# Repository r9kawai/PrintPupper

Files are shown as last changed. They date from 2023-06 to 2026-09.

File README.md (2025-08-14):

# PrintPupper  
## Release v0.2 2025 Aug 14
PrintPupper is an open-source quadruped robot that anyone can build. It is based on Pupper, developed by Stanford University, and has been redesigned to be cheaper and easier to build. With just a 3D printer and inexpensive parts, you can build a full-fledged quadruped robot with 12 joints.  
PrintPupper は誰でも作れるオープンソースの四足歩行ロボットです。スタンフォード大学の開発したPupperを元に、より安価に簡単に作れるよう再設計しました。3Dプリンタと安価な部品だけで12自由度の本格四足ロボを作れます。
  
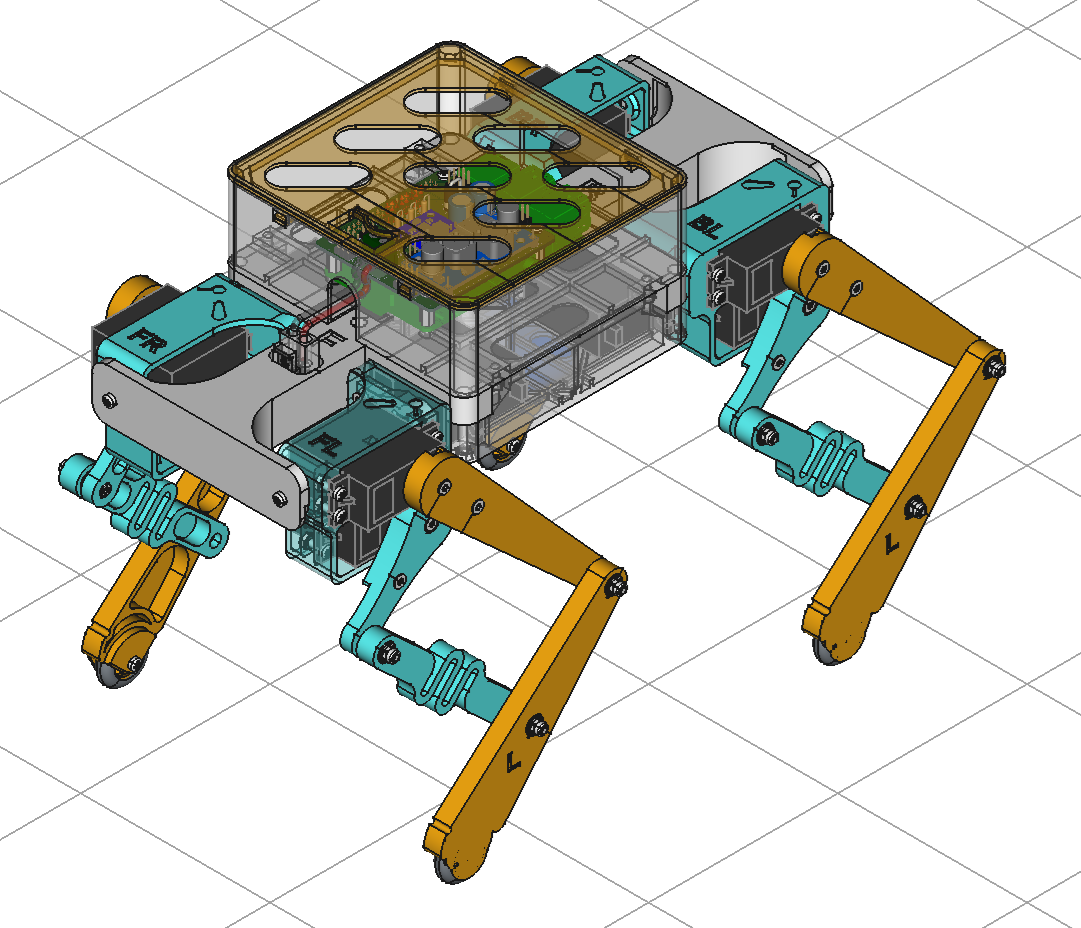
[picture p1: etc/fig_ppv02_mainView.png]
  
  
## printpupper.com  
[https://www.printpupper.com/](https://www.printpupper.com/)  
This portal site explains the assembly procedure with detailed figs.
このポータルサイトでは組立手順を詳細な図で説明しています。
  
・3DプリンターとAmazonで容易に入手できる安価な部品だけで作れる。  
・組立手順をWebで詳細に説明。  
・FreeCAD設計データ、KiCAD基板設計データなど全てGitHubで公開。  
・オリジナル設計よりも頑丈で壊れにくい。  
・USBジョイパッド対応。  
・キャリブレーション作業がジョイパッドだけで可能。  
・RC用大容量バッテリー搭載可能で40分の連続歩行。  
・拡張性あり、改造が容易、IMU搭載が可能。  
・Raspberry Pi 3以降または、Raspberry Pi Zero 2 W での作成が可能。  
  
・Can be built using only a 3D printer and inexpensive parts readily available on Amazon.  
・Assembly instructions are explained in detail on the Web.  
・FreeCAD design data, KiCAD board design data, etc. are all available on GitHub.  
・Sturdier and less likely to break than the original design.  
・Compatible with USB joypad.  
・Calibration can be done using only the joypad.  
・Can be equipped with a large-capacity RC battery for 40 minutes of continuous walking.  
・Expandable, easy to modify, and can be equipped with an IMU.  
・Can be built with a Raspberry Pi 3 or later, or a Raspberry Pi Zero 2 W.

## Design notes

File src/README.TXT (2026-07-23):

# If you choose 270deg servo, please "touch _servo_type_270deg"

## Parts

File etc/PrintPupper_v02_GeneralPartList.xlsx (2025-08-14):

PrintPupper_v02_GeneralPartList | 一般部品リスト
Class 分類 | Name | 名称 | Qua / 数量 | in 4leg | in torso | in stand
Servo motor サーボモーター | DS3235 180deg 35kg core less servo | DS3235 180度35KGコアレスサーボ | 12
 | ※ needs the attached metal horn in servo | ※ 付属の金属ホーンが必要
Metal parts 金属部品 | M3 Hex nut | M3 六角ナット | 64 | 48 | 14 | 2
 | M3 Nylon hex nut | M3 ナイロン六角ナット | 12 | 12
 | M3 10mm countersunk hex cap screw | M3 10mm 六角穴皿ボルト | 24 | 24
 | M3 10mm truss-head screw | M3 10mm トラス頭ネジ | 50 | 40 | 8 | 2
 | M3 20mm hex cap screw | M3 20mm 六角穴ボルト | 18 | 12 | 6
 | 693ZZ Ball bearing 3x8x4mm | 693ZZ ボールベアリング | 28 | 28
 | M2.5 8mm screw | M2.5 8mm ねじ | 8 |  | 8
 | M2.5 12mm hex spacer | M2.5 12mm 六角スペーサー | 4 |  | 4
※ in use RaspiZero | M2.5 Hex nut | M2.5 六角ナット | 2 |  | 2
 | Servo horn (Attached in servo) | サーボホーン (サーボ付属品) | 12 | 12
 | M2 8mm hex cap screw (Attached in servo) | M2 8mm 六角穴ボルト (サーボ付属品) | 24 | 24
Rubber parts ゴム部品 | Rubber in Dia 16mm Out 25mm | ゴムグロメット内径16mm外径25mm相当品 | 4
 | equivalent item
PCB parts プリント基板部品 | Main PCB | メイン基板 | 1
 | XL6009 boost back DC-DC converter | XL6009昇降圧DCDCコンバータ | 1
 | Resistor 1k ohm 0.25W | 抵抗 1kオーム 0.25W | 3
 | Electrolytic condenser 2200uF 16V | 電解コンデンサ 2200uF 16V | 2
 | Schottky Barrier Diode 1N5820 | ショットキーバリアダイオード 1N5820 | 1
 | LED red | LED 赤 | 1
 | LED green | LED 緑 | 1
 | LED blue | LED 青 | 1
 | Terminal block 2contact 5.08mm pitch | ターミナルブロック 2端子 5.08mmピッチ | 1
 | Pin header 2.54mm pitch 40pin 1 row | ピンヘッダ 2.54mmピッチ 40ピン 1列 | 2
 | 40(2x20)pin header socket | 40(2x20)ピンヘッダソケット | 1
 | Tamiya bat connecter harness male | タミヤバッテリコネクタハーネス(オス) | 1
CPU board CPUボード | Raspberry Pi "3" or "4" or "Zero 2 W" | ラズベリーパイ 3または4またはZero 2 W | 1
 | ※ Zero W is NG
Battery バッテリー | 2S 7.4v LiPo battery (Tamiya) | 2S 7.4v リポバッテリー タミヤコネクタ | 1
 | 7.2v NiCd Battery Pack Tamiya compatible | 7.4v タミヤニッカドバッテリー互換品
 | 製品例 Choice cases | GOLDBAT 4000mAh 2S 7.4V Lipo TAMIYA Plug
※ Option オプション | MPU6050 accelerometer gyro sensor | MPU6050加速度センサー | 1
Controller コントローラ | エレコム ゲームパッド JC-U3912TBK |  | 1
 | PS4 Controller (DUAL SHOCK4) | PS4 コントローラ (DUAL SHOCK4)
 | ※ Worked with compatible products. | ※ 互換品でも動作しました。
 |  | Total | 282

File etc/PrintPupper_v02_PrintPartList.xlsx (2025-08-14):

PrintPupper_v02_PrintPartList | 印刷部品リスト
File name | Name | 名称 | Qua / 数量
01_print_knee_horn_4pcs.step | Knee horn | 膝ホーン | 4
02_print_upper_leg_4pcs.step | Upper leg | 上脚 | 4
03_print_knee_linkage_4pcs.step | Knee linkage | 膝リンク | 4
04_print_lower_leg_L_2pcs.step | Lower leg L | 下脚R | 2
05_print_lower_leg_R_2pcs.step | Lower leg R | 下脚L | 2
06_print_lower_leg_cap_4pcs.step | Lower leg cap | 下脚キャップ | 4
07_print_coxa_FL_1pcs.step | Coxa FL1 | 股関節FL | 1
08_print_coxa_FR_1pcs.step | Coxa FR1 | 股関節FR | 1
09_print_coxa_BL_1pcs.step | Coxa BL1 | 股関節BL | 1
10_print_coxa_BR_1pcs.step | Coxa BR1 | 股関節BR | 1
11_print_center_torso_1pcs.step | Center torso | 中央胴体 | 1
12_print_front_torso_1pcs.step | Front torso | 前胴体 | 1
13_print_back_torso_1pcs.step | Back torso | 後胴体 | 1
14_print_battery_holder_2pcs.step | Battery holder | バッテリホルダ | 2
15_print_pcb_box_1pcs.step | PCB box | PCB箱 | 1
16_print_pcb_box_lid_1pcs.step | PCB box lid | PCB箱蓋 | 1
17_print_stand_upper_1pcs.step | Stand upper | スタンド上 | 1
18_print_stand_lower_1pcs.step | Stand lower | スタンド下 | 1
19_print_calibration_plate_1pcs.step | Calibration plate | キャリブプレート | 1
 |  | Total | 34

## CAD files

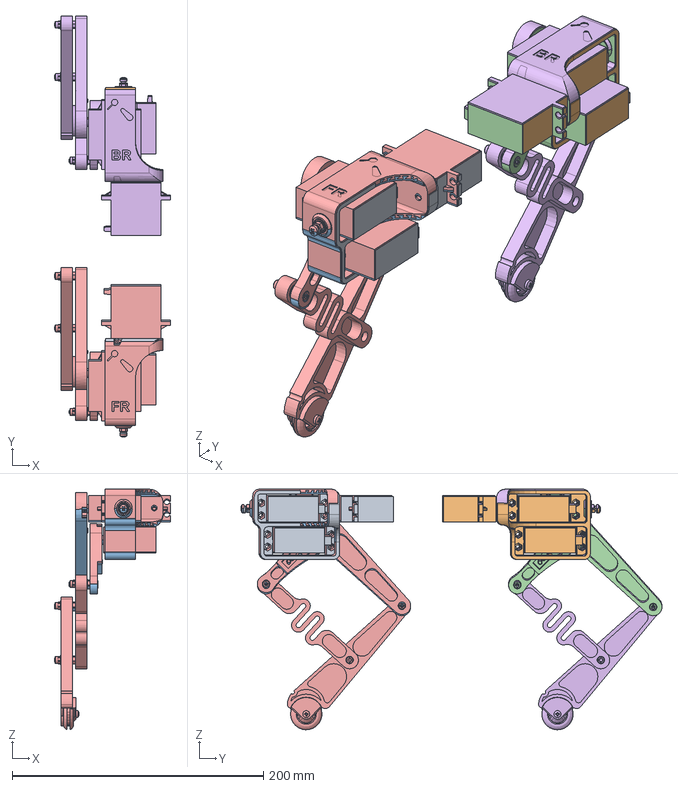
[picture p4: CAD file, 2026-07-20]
freecad/PrintPupper_v02_0_StdAssembly.FCStd
92.6 x 335.1 x 191.6 mm
GeoCheckFR_0
GeoCheckBR_0
GeoCheckFR_1
GeoCheckBR_1
GeoCheckFR_2
GeoCheckBR_2

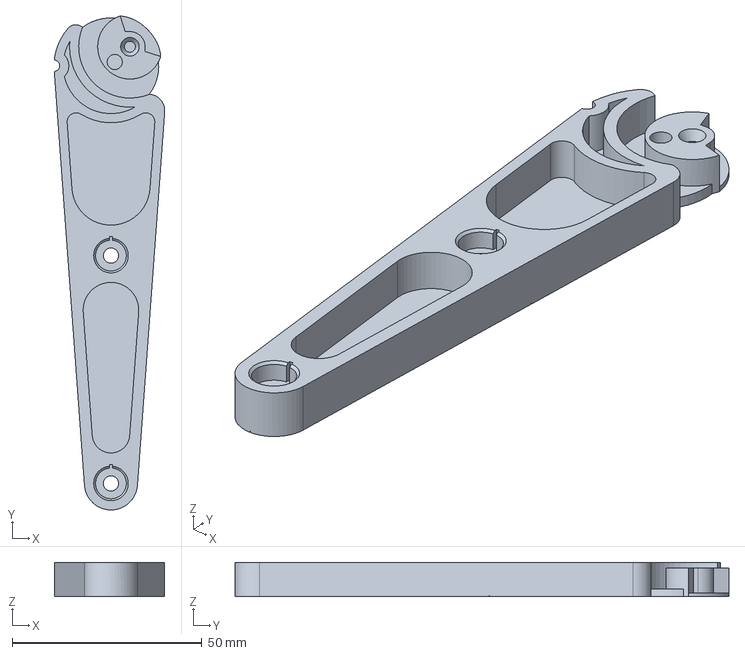
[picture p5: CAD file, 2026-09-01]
freecad/exportSTEP/04_new_print_lower_leg_L_2pcs.step
29.1 x 130.1 x 9.00 mm

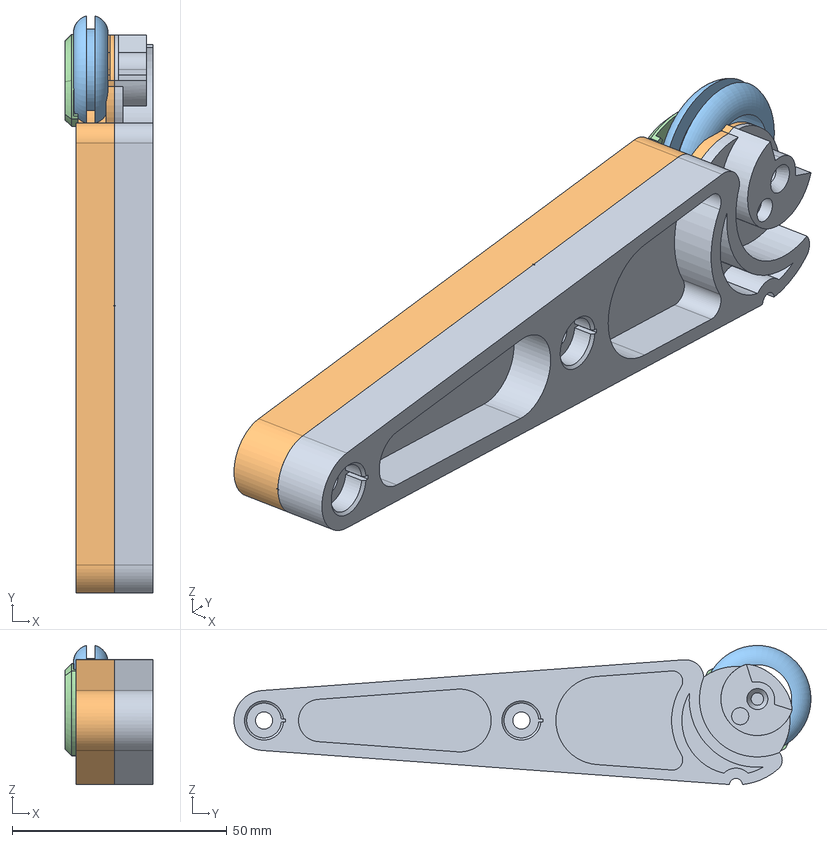
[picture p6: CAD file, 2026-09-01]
freecad/PrintPupper_v02_lowerLegImproved.FCStd
20.5 x 134.5 x 32.4 mm
print_lower_leg4_R
print_lower_leg4_L
parts_rubber_grommet_In16_Out25_T25mm
print_lower_leg_cap4_

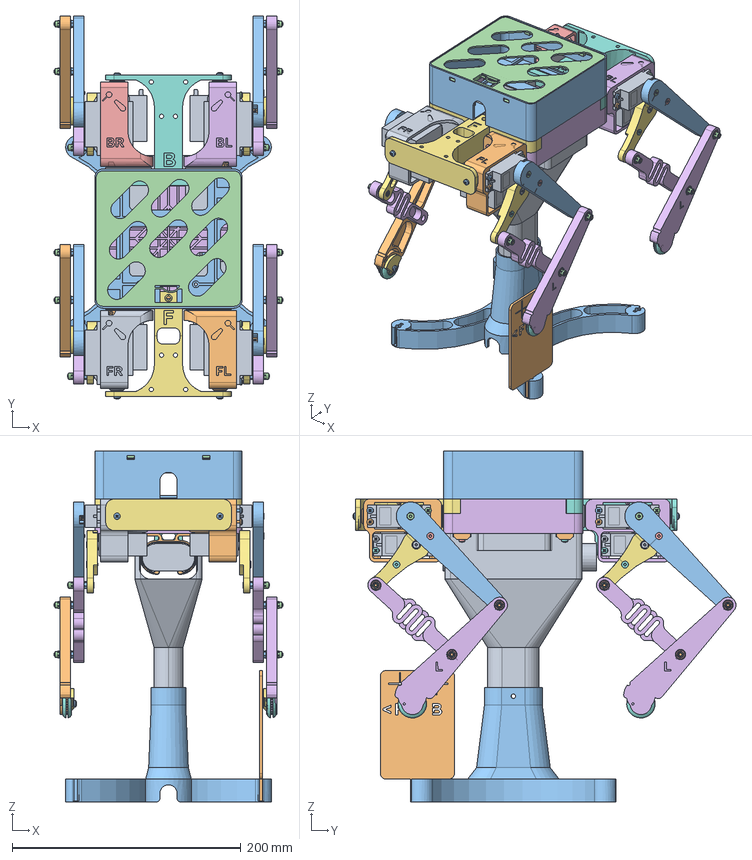
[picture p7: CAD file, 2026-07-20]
freecad/PrintPupper_v02_0.FCStd
200.0 x 335.1 x 307.0 mm
parts_servo x 12
M3x20-Screw x 12
M3-Nut x 16
M3-Nut026 x 12
ball_bearing_3x8x4mm x 28
print_lower_leg3_L x 2
print_lower_leg_cap3_ x 4
parts_rubber_grommet_In16_Out25_T25mm x 4
M3x10-Screw169 x 2
parts_servo_horn x 10
print_upper_leg x 4
M3x10-Screw153 x 2
M3x10-Screw154 x 2
print_knee_linkage_damp x 4
print_knee_horn x 4
M3x10-Screw155 x 2
M3x10-Screw156 x 2
print_coxa_FL
M3x10-Screw114 x 4
M3x10-Screw157 x 2
M3x10-Screw158 x 2
M3x10-Screw159 x 2
M3x10-Screw160 x 2
M3x10-Screw161 x 2
M3x10-Screw162 x 2
M3x10-Screw163 x 2
M3x10-Screw164 x 2
M3-Nut043 x 2
M3-Nut044 x 2
M3-Nut045 x 2
M3-Nut046 x 2
M3-Nut047 x 2
M3-Nut048 x 2
M3-Nut049 x 2
M3-Nut050 x 2
M3x10-Screw165
M3x10-Screw166
print_coxa_BL
M3x10-Screw167
M3x10-Screw168
print_coxa_FR
print_lower_leg3_R x 2
_M3x10_PanHeadScrew x 2
_M3x10_FlatBolt x 8
print_coxa_BR
print_center_torso
print_front_torso
print_back_torso
parts_BatteryLipo2S7.4V4000mAh
print_battery_holder x 2
print_pcb_box
print_pcb_box_lid
M3x10-Screw147
M3x10-Screw148
M3x10-Screw149
M3x10-Screw150
print_stand_upper
print_calibration_plate
print_stand_lower

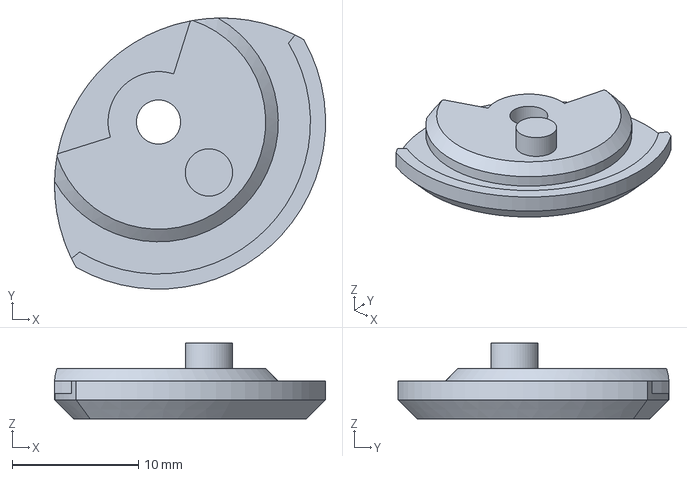
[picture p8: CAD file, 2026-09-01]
freecad/exportSTEP/06_new_print_lower_leg_cap_4pcs.step
21.5 x 21.5 x 6.00 mm

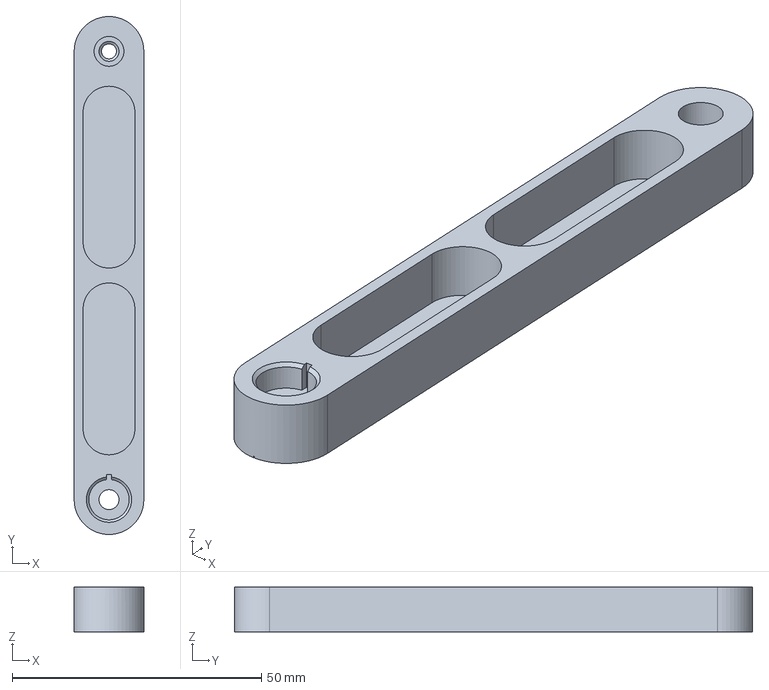
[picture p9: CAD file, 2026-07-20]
freecad/exportSTEP/03_print_knee_linkage_4pcs_Rigid.step
14.0 x 104.0 x 9.00 mm

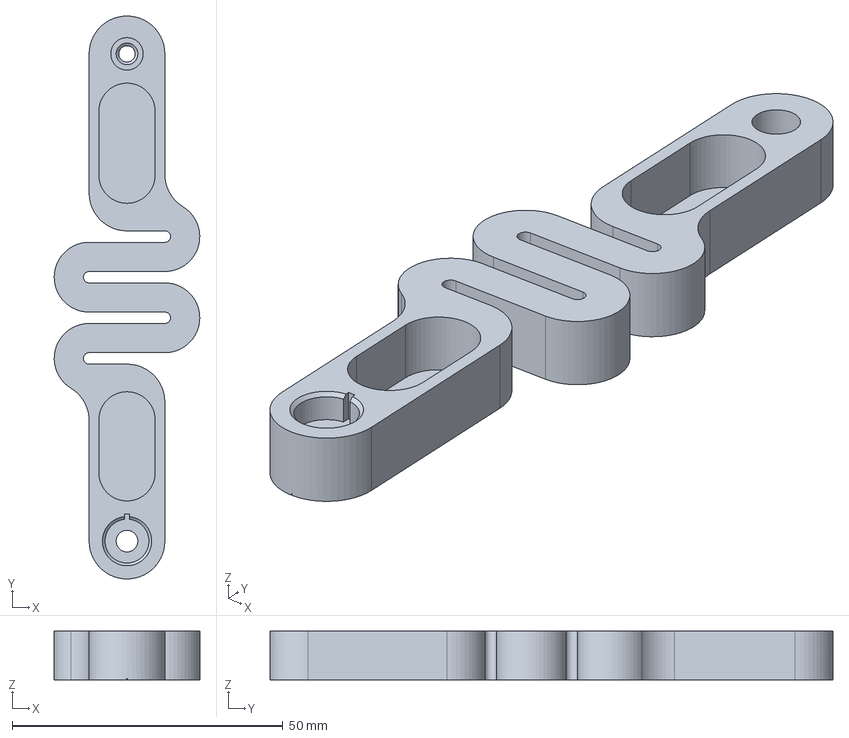
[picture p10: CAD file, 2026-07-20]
freecad/exportSTEP/03_print_knee_linkage_4pcs_Hard.step
26.9 x 104.0 x 9.00 mm

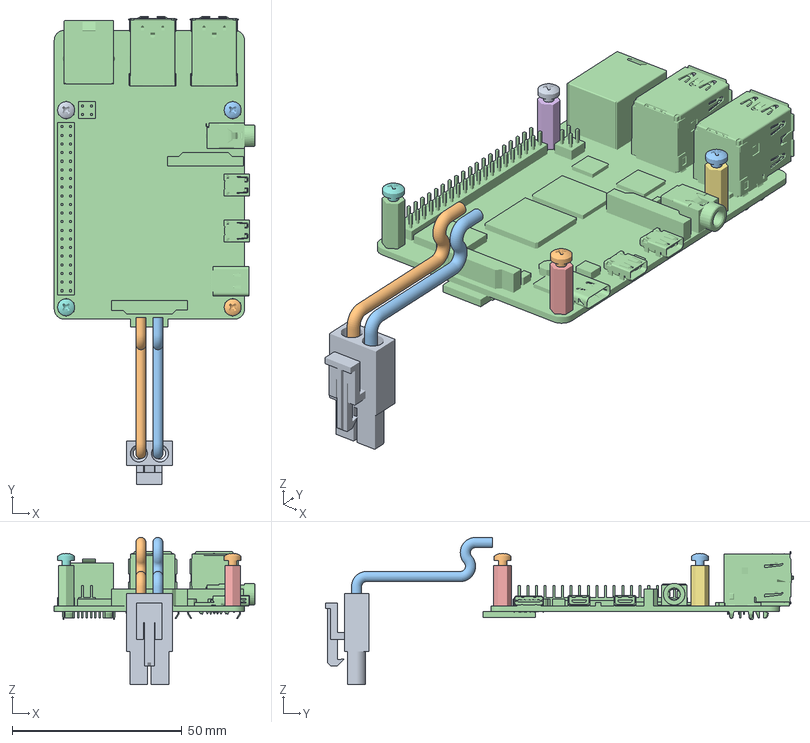
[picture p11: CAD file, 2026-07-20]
freecad/PrintPupper_v01_v02_PCBs.FCStd
59.0 x 137.7 x 43.3 mm
TamiyaMaleConnector
hexspacer_M2.5_12mm
hexspacer_M2.5_12mm001
hexspacer_M2.5_12mm002
hexspacer_M2.5_12mm003
M2.5x8-Screw014
M2.5x8-Screw015
M2.5x8-Screw016
M2.5x8-Screw017
raspberry_pi_4

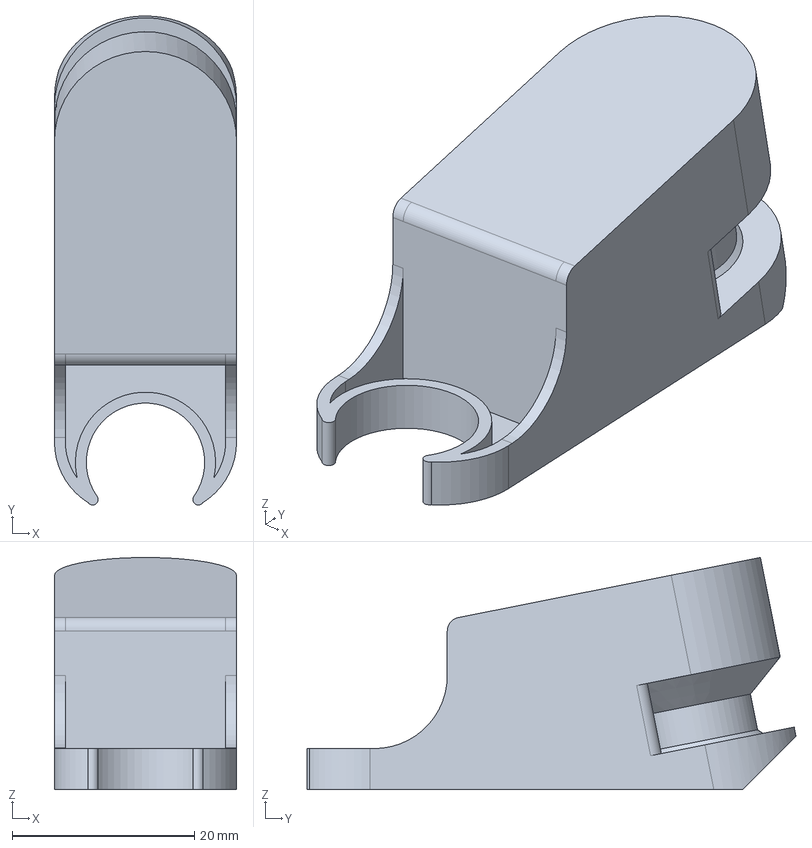
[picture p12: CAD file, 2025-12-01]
freecad/exportSTEP/27_print_deco_tail_node_6pcs.step
20.0 x 53.7 x 25.5 mm

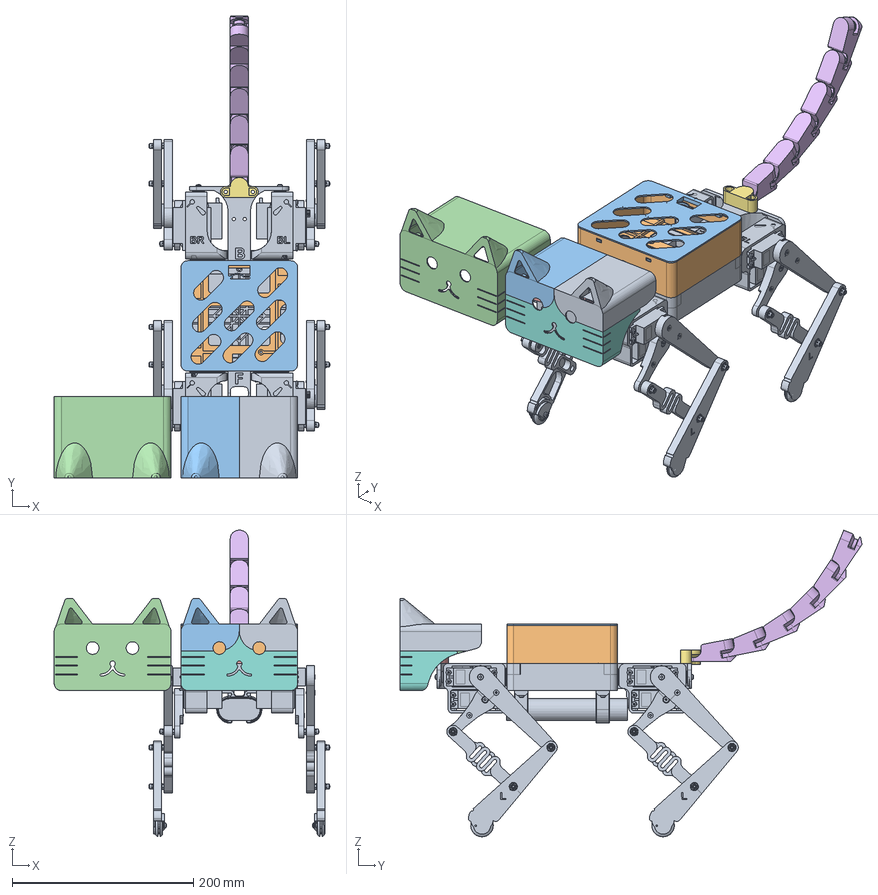
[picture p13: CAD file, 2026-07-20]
freecad/PrintPupper_v02_0_Decoration.FCStd
304.5 x 510.3 x 338.8 mm
Robot_Solid
print_pcb_box_1pcs_Solid
print_pcb_box_lid_1pcs_Solid
print_deco_head
print_deco_head_stay
print_deco_tail_node x 6
print_deco_tail_base
print_deco_head_tricolor_c1
print_deco_head_tricolor_c2
print_deco_head_snap_ring x 4
print_deco_head_tricolor_c3

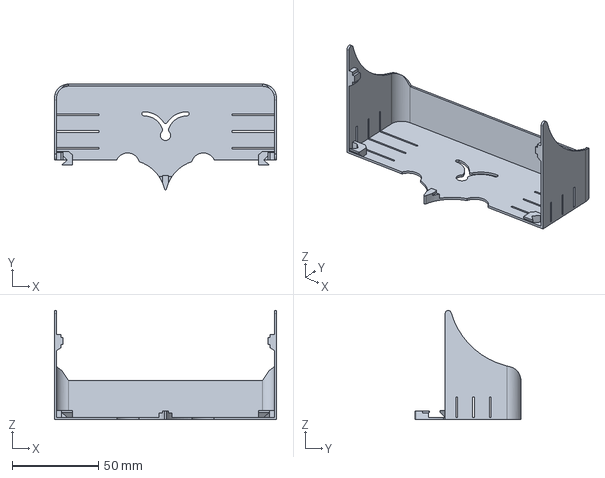
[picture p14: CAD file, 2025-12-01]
freecad/exportSTEP/22_print_deco_head_triC1_1pcs.step
129.0 x 61.4 x 63.4 mm

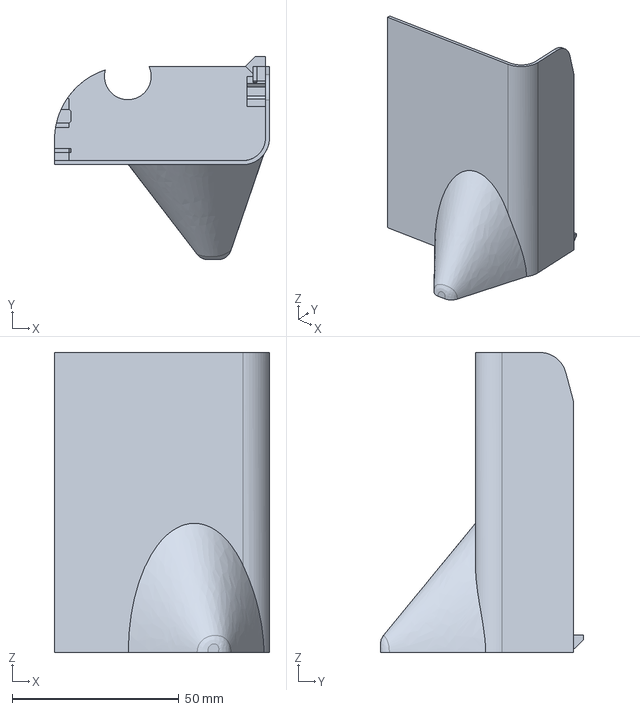
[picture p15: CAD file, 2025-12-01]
freecad/exportSTEP/23_print_deco_head_triC2_1pcs.step
64.5 x 61.0 x 90.0 mm

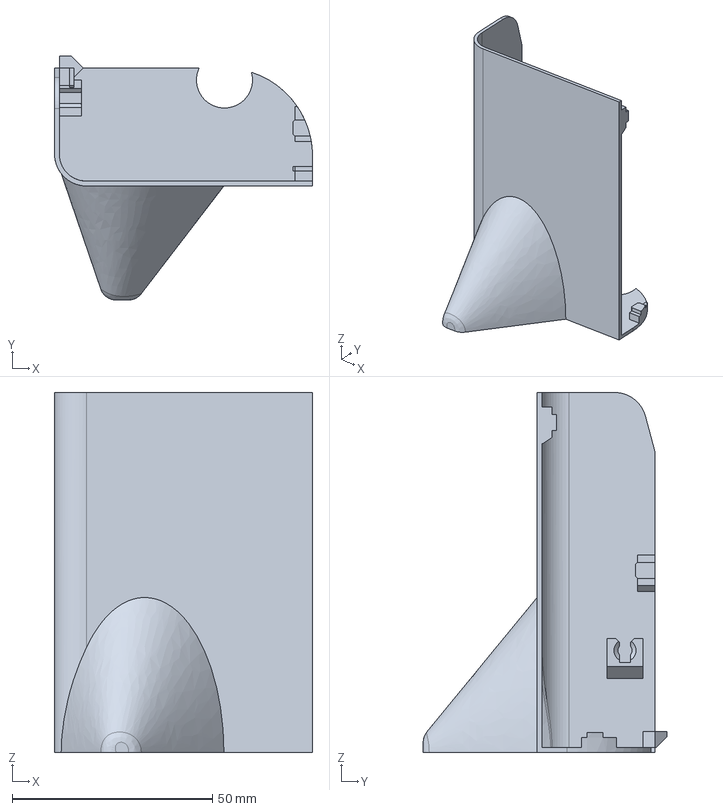
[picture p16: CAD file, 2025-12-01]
freecad/exportSTEP/24_print_deco_head_triC3_1pcs.step
64.5 x 61.0 x 90.0 mm

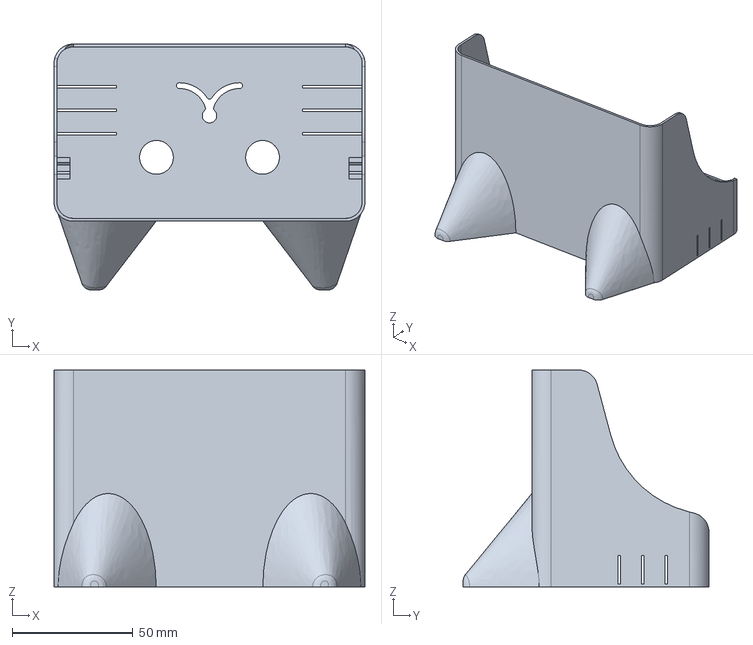
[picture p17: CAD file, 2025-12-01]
freecad/exportSTEP/20_print_deco_head_1pcs.step
129.0 x 102.0 x 90.0 mm

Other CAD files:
freecad/exportSTEP/05_new_print_lower_leg_R_2pcs.step
freecad/PrintPupper_v02_0_GeoCheckFL_YZ.FCStd
freecad/exportSTEP/25_print_deco_head_triSnap_4pcs.step
freecad/exportSTEP/21_print_deco_head_stay_1pcs.step
freecad/exportSTEP/01_print_knee_horn_4pcs.step
freecad/exportSTEP/02_print_upper_leg_4pcs.step
freecad/exportSTEP/03_print_knee_linkage_4pcs.step
freecad/exportSTEP/04_print_lower_leg_L_2pcs.step
freecad/exportSTEP/05_print_lower_leg_R_2pcs.step
freecad/exportSTEP/06_print_lower_leg_cap_4pcs.step
freecad/exportSTEP/07_print_coxa_FL_1pcs.step
freecad/exportSTEP/08_print_coxa_FR_1pcs.step
freecad/exportSTEP/09_print_coxa_BL_1pcs.step
freecad/exportSTEP/10_print_coxa_BR_1pcs.step
freecad/exportSTEP/11_print_center_torso_1pcs.step
freecad/exportSTEP/12_print_front_torso_1pcs.step
freecad/exportSTEP/13_print_back_torso_1pcs.step
freecad/exportSTEP/14_print_battery_holder_2pcs.step
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

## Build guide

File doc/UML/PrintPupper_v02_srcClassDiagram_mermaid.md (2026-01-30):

```mermaid

classDiagram
direction LR

%% =========================
%% Entry points / Processes
%% =========================
class run_robot_py["run_robot.py\n(entrypoint)"] {
  +main()
  +control_loop()
}

class joystick_py["PupperCommand/joystick.py\n(subprocess entry)"] {
  +main()
  +read_joystick()
  +send_command()
  +recv_led()
}

%% =========================
%% Command / State / Config
%% =========================
class Command {
  +horizontal_velocity
  +yaw_rate
  +height
  +pitch
  +roll
  +activate_event
  +trot_event
  +hands_event
  +caliblate_mode_event
  +rx_ry_switch
  +auto_trot
}

class State {
  +ticks
  +behavior_state
  +foot_locations
  +joint_angles
  +imu_roll_pitch_yaw
  +...
}

class Config {
  +robot_params
  +gait_params
  +swing_params
  +stance_params
  +pwm_params
  +servo_calibration
}

class PWMParams {
  +pins : np.array(3x4)
  +pwm_freq
  +pwm_range_usec
}

class ServoCalibration {
  +NEUTRAL_ANGLE_DEGREES : np.array(3x4)
  +SERVO_MULTIPLIERS : np.array(3x4)
}

%% =========================
%% Input Interface (TCP)
%% =========================
class JoystickInterface {
  -sock
  -last_joymsg
  +get_command(state) Command
  +set_led_color(r,g,b)
}

%% =========================
%% Core controller (FSM)
%% =========================
class Controller {
  -gait_controller
  -stance_controller
  -swing_controller
  +run(state, command)
  +step_trot(state, command)
  +step_rest(state, command)
  +step_hands(state, command)
}

class GaitController {
  +update(state, command)
  +contact_modes
  +phase
}

class StanceController {
  +run(state, command, contact_modes)
  +foot_locations_stance
}

class SwingLegController {
  +run(state, command, contact_modes)
  +foot_locations_swing
}

%% =========================
%% Kinematics / Geometry
%% =========================
class Kinematics {
  +four_legs_inverse_kinematics(foot_locations) joint_angles(3x4)
  +leg_inverse_kinematics(...)
}

class NonparallelKneeCompute {
  +compute(leg_angle, knee_angle, mirror) knee_servo_angle
}

%% =========================
%% Hardware Output (pigpio)
%% =========================
class HardwareInterface {
  -pigpio
  -pwm_params
  -servo_calibration
  +initialize_pwm()
  +set_actuator_positions(joint_angles)
  +angles_to_pwm(joint_angles) pwm_usec(3x4)
  +extrapolation_unparallel_actuator_positions(joint_angles) joint_angles'
}

%% =========================
%% Relationships (Main process)
%% =========================
run_robot_py --> Config : loads
run_robot_py --> State : owns
run_robot_py --> JoystickInterface : polls
run_robot_py --> Controller : runs
run_robot_py --> HardwareInterface : outputs

JoystickInterface --> Command : creates
Controller --> State : updates
Controller --> Command : reads

Controller o-- GaitController
Controller o-- StanceController
Controller o-- SwingLegController

Controller --> Kinematics : IK
HardwareInterface --> PWMParams
HardwareInterface --> ServoCalibration
HardwareInterface --> NonparallelKneeCompute : knee remap

%% =========================
%% Subprocess relationships
%% =========================
joystick_py ..> JoystickInterface : TCP localhost\npickle dict

```

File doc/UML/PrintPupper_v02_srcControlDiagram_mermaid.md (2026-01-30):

```mermaid

sequenceDiagram
autonumber
participant joy as joystick.py (sub)
participant jsdev as Joystick Device
participant tcp as TCP localhost
participant jif as JoystickInterface (main side)
participant main as run_robot.py
participant ctrl as Controller
participant gait as GaitController
participant stance as StanceController
participant swing as SwingLegController
participant kin as Kinematics
participant hw as HardwareInterface
participant knee as NonparallelKneeCompute
participant pig as pigpio
participant servos as 12 Servos

loop ~15Hz (MESSAGE_RATE)
  %% --- Subprocess reads joystick and sends joymsg ---
  joy->>jsdev: read axes/buttons
  joy->>joy: build joymsg(dict)\n+ long-press detection
  joy->>tcp: send(pickle.dumps(joymsg))

  %% --- Main process receives and converts to Command ---
  main->>jif: get_command(state)
  jif->>tcp: select()/recv (non-blocking)
  tcp-->>jif: joymsg(pickled dict)
  jif->>jif: decode joymsg / edge-detect events
  jif-->>main: Command\n(vx,vy,yaw,height,pitch,events...)

  %% --- Controller state machine ---
  main->>ctrl: run(state, command)
  alt behavior_state == TROT
    ctrl->>gait: update(state, command)\nphase/contact_modes
    ctrl->>stance: run(state, command, contact_modes)
    ctrl->>swing: run(state, command, contact_modes)
    stance-->>ctrl: foot_locations_stance(3x4)
    swing-->>ctrl: foot_locations_swing(3x4)
    ctrl->>ctrl: merge -> foot_locations(3x4)\n+ body rotation compensation
    ctrl->>kin: four_legs_inverse_kinematics(foot_locations)
    kin-->>ctrl: joint_angles(3x4)\n(axis0,1,2=knee angle beta)
  else behavior_state == REST/HANDS/DEACT
    ctrl->>ctrl: generate rest/hands pose
    ctrl->>kin: (if needed) IK / direct angles
    kin-->>ctrl: joint_angles(3x4)
  end
  ctrl-->>main: state.joint_angles updated

  %% --- Hardware output + knee remap ---
  main->>hw: set_actuator_positions(state.joint_angles)
  hw->>hw: extrapolation_unparallel_actuator_positions()
  loop 4 legs
    hw->>knee: compute(leg, knee, mirror)\n-> knee_servo_angle
    knee-->>hw: kneeX
  end
  hw->>hw: angles_to_pwm()\nneutral + multipliers + linear map
  loop 12 channels
    hw->>pig: set_PWM_dutycycle(gpio, pwm_usec)
  end
  pig-->>servos: PWM (500-2500us equiv)\n-> servo angles

  %% --- Optional LED feedback (bi-directional) ---
  main->>jif: set_led_color(r,g,b) (optional)
  jif->>tcp: send(led_color)
  tcp-->>joy: recv led_color
  joy->>jsdev: set controller LED
end

```

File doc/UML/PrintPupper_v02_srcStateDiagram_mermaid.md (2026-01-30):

```mermaid

stateDiagram
    [*] --> DEACT

    DEACT --> REST : activate_event
    REST --> DEACT : activate_event

    REST --> TROT : trot_event
    TROT --> REST : trot_event

    REST --> HANDS : hands_event
    HANDS --> REST : hands_event

    %% auto trot
    REST --> TROT : auto_tro speed > th
    TROT --> REST : auto_tro speed <= th

    %% calibration
    DEACT --> CALIBRATE : caliblate ope
    CALIBRATE --> DEACT : exit

```

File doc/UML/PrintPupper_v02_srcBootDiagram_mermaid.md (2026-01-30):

```mermaid

sequenceDiagram
autonumber
participant systemd as systemd
participant joy as PupperCommand/joystick.py (sub)
participant jsdev as Joystick Device
participant tcp as TCP localhost:51000
participant main as run_robot.py (main)
participant jif as JoystickInterface
participant cfg as Config
participant hw as HardwareInterface
participant pig as pigpiod

systemd->>joy: start joystick.service
joy->>jsdev: open /dev/input/js0 or PS4 interface
joy->>tcp: listen(51000)
joy->>tcp: accept() wait for client

systemd->>pig: start pigpiod (ExecStartPre)
systemd->>main: start robot.service

main->>cfg: load Config / Params
main->>hw: HardwareInterface(config)
hw->>pig: connect pigpio daemon
hw->>pig: set_PWM_frequency(range=10000, freq=100Hz)\nfor 12 pins
main->>jif: JoystickInterface()
jif->>tcp: connect(localhost:51000)
tcp-->>joy: connection established

```

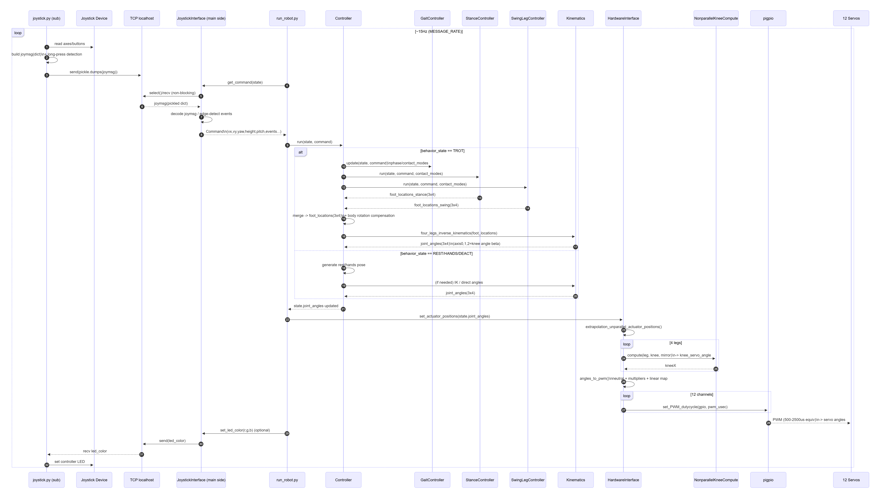
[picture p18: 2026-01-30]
doc/UML/PrintPupper_v02_srcControlDiagram_mermaid.png

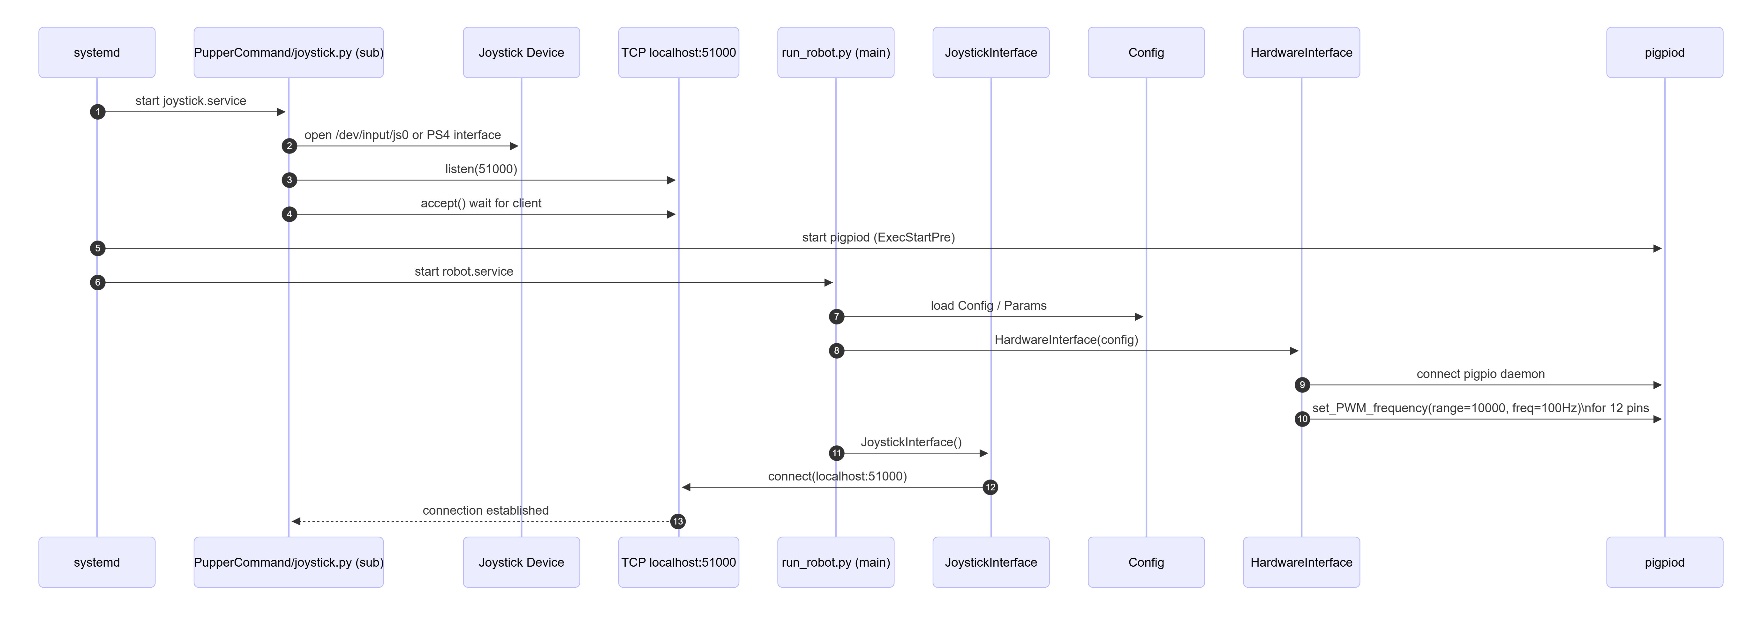
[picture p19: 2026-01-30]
doc/UML/PrintPupper_v02_srcBootDiagram_mermaid.png

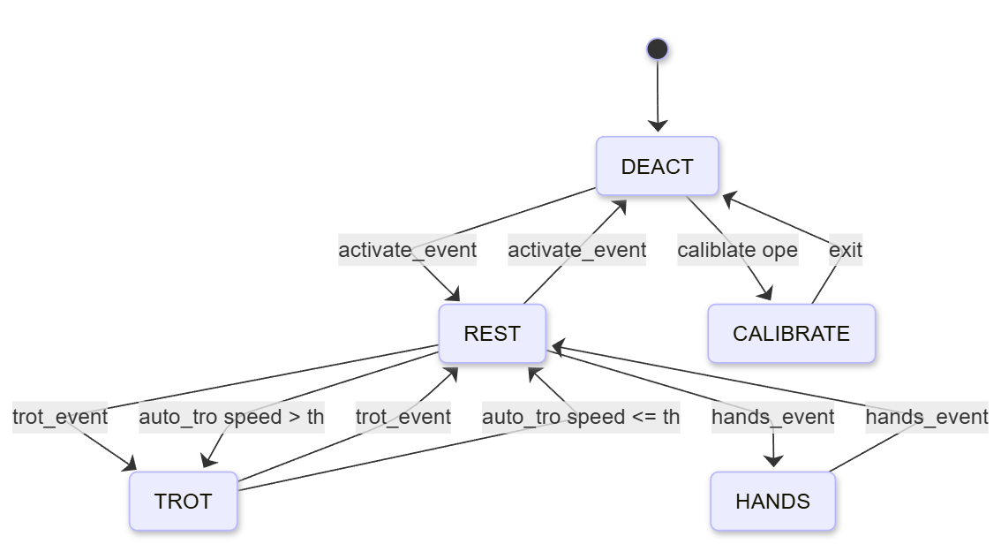
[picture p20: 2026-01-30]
doc/UML/PrintPupper_v02_srcStateDiagram_mermaid.png

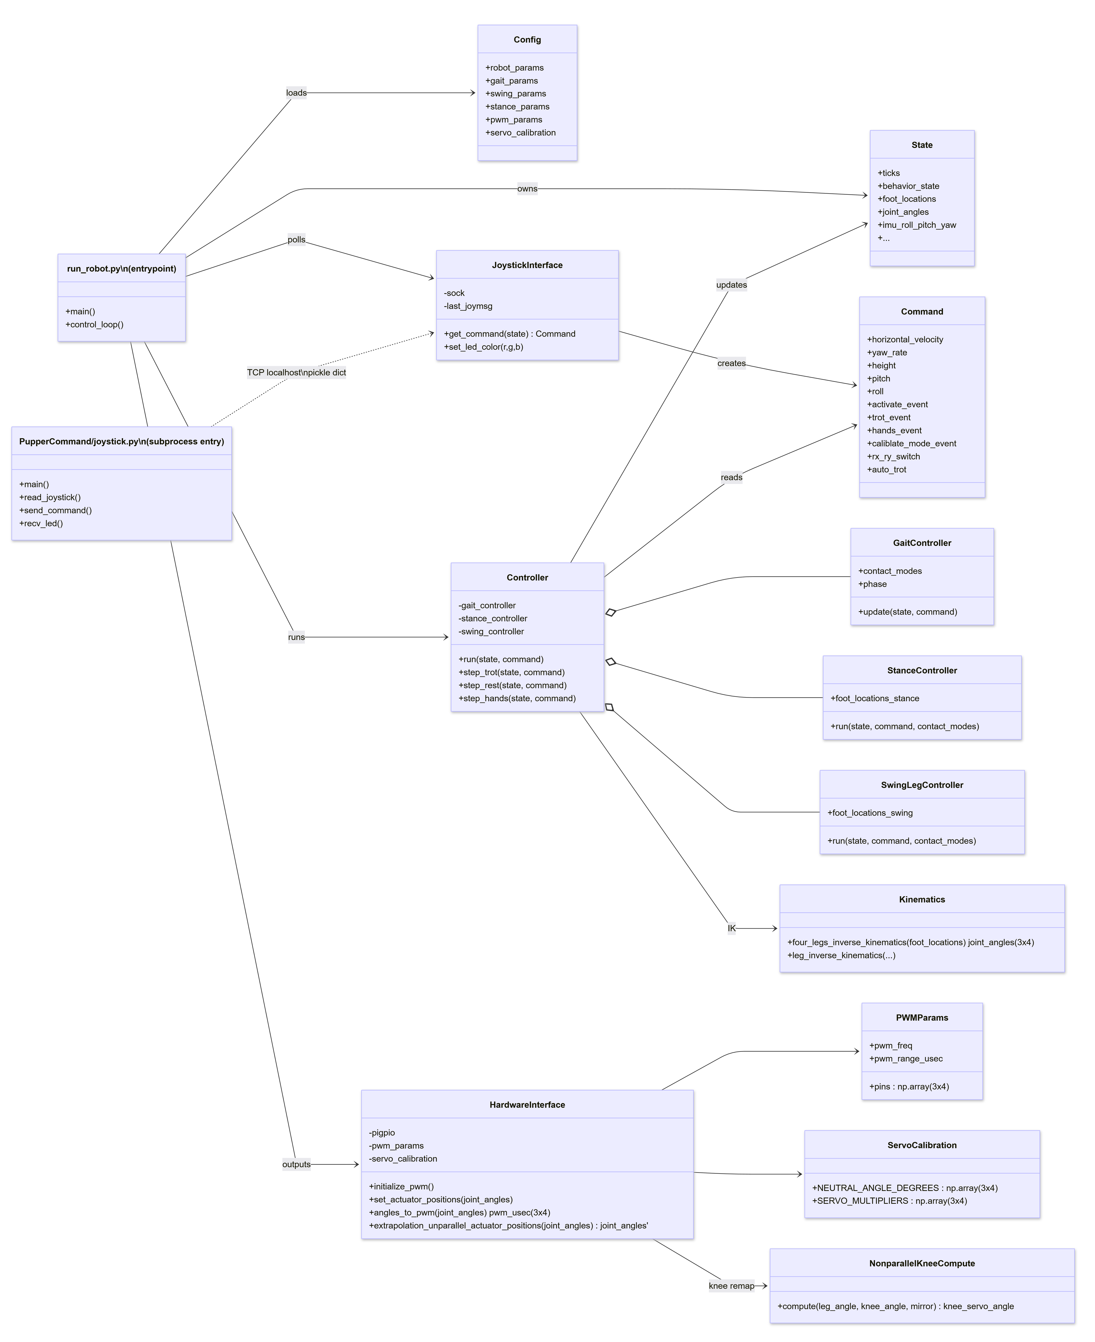
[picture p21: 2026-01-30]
doc/UML/PrintPupper_v02_srcClassDiagram_mermaid.png

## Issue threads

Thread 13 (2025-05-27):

歩行時の姿勢を安定化させる方法について

noritsune, 2025-05-27:
はじめまして。最近、PrintPupperを作って遊んでいる者です。
歩行時の姿勢がぐらついてすぐに転んでしまうので、どうすれば改善できるかこのところ悩んでいます。

滑らかな床ですと概ね問題なく歩けます。しかし、急なスティック操作をするとひっくり返ってしまいます。
また、アスファルトや芝生など凸凹していたり、摩擦が大きな平面ですとすぐにひっくり返ってしまい。まともに歩くことが出来ません。この問題はPrintPupperの足先が歩行時にほとんど床面から離れずすり足の様に動くことが原因だと思われます。

そもそも現状のPrintPupperの設計自体が悪路での歩行を目標としていないのではないかなと推測しつつ、私としては屋外で本物の犬と同じ様に振る舞うロボットになれば理想だなと思い改善を試みています。

うまくいった変更の一つに、足踏みの高速化があります。動作の様子は以下のリンクからご覧になれます。
https://x.com/noritsunetsune/status/1927388802164650231

Config.pyに記載されているパラメータ－を以下の通り変更しました。
- z_clearance: 0.08→0.16
- overlap_time: 0.20→0.10
- swing_time: 0.12→0.06

上記の変更では足踏みのサイクル速度を倍速にすることで、体勢が崩れる前に次の足を踏み出すことで安定した歩行ができるようになったと理解しています。

制作者さんの方で歩行時の姿勢の安定化についてどう考えられているかと、上記の変更が良いアプローチなのかご意見をお聞きしたいです。

PS. このIssueを立てる前にcommitツリーを眺めていたところ、偶然昨日時点で久しぶりにcommitが追加されているのを見つけました。バージョンアップ版の開発を始められたんでしょうか？気になっています。

r9kawai, 2025-05-30:
PrintPupperに興味を持っていただきありがとうございます！

PrintPupperについては、現在大幅なアップデートv0.2（再々設計）が開発中です。
v0.1の歩行安定性の低さは問題だと思っていて、正直いろいろと未熟な点があると思います。
v0.2はv0.1と電気的には同じ部品（メイン基板、サーボモータ、ラズパイ、バッテリー）を使用し、
プリント部品とソフトが刷新される予定です。
v0.1を作って頂けた方は、解体して3Dプリント部品を刷り直せば（小ねじ類程度の買い足しで）v0,2を作れる予定です。
新リンク機構により歩行も安定し、かつ組立も容易になる計画です。今年夏ぐらいの予定で開発中です！
将来的にはROS/Champ対応を目指しています。（流行のAI歩容生成技術と繋がれるようになる）

なので、v0.2の公開を待っていただけると幸いです。
以上、よろしくお願いいたします。

2025年5月28日(水) 0:49 noritsune ***@***.***>:

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

r9kawai, 2025-05-30:
追伸、
default_z_ref という値があり、これは起動時の高さ（マイナスのメートル表記）を指定しています。
これを変えて少し低め／高めにすると良いかもしれません。
z_clearance は歩行時に足を上げる高さを示していて、0.08は80mmになります。
あまり高くしてもサーボが反応できないのでむしろ低くした方が良いかもしれません。
self.x_shiftを変えると起立状態で足を下ろす位置を前後方向に変えることができます。
self.x_shift = 0.005 とすると、足を少し前方に降ろすようになります。マイナス値だと後方になります。
これらは全て0.001で1mmです。

ただ、パラメータ地獄になってしまうので、
根本的に設計を変えないと大きく改善しないと考えており、v0,2では大幅に良くなると思います。

2025年5月30日(金) 12:26 河合竜次 ***@***.***>:

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

noritsune, 2025-05-30:
パラメーター設定についてのアドバイスありがとうございます。まさに私は最近パラメーター地獄に陥っています。先述の高速足踏みパラメーターで安定はしたので、その上で移動や旋回を高速にしようと別のパラメーターを編集したら高速に歩けるようになりましたがその代わりに再びすぐ転ぶようになりました。

v0.2の公開を楽しみにしています。公開されたらぜひパーツをプリントして試してみたいです。強化学習での歩容生成にそろそろ挑戦しようと考えていたのでROS対応は嬉しいです。そもそも、ラズパイでスペック的に推論ができる
かとか、トルクセンサーなどが無くても大丈夫かな？など不安もありますが。

ところで、歩行の安定化の別アプローチとしてこれからIMUの搭載を試してみるところです。今日届きます。現状のプログラムを見ると、IMUからの入力を元にトロット時の姿勢が補正されるようなので歩行が安定するかなと思っているんですがどうでしょうか？

noritsune, 2025-05-30:
現状のコードだと全然だめなのですね…
カルマンフィルタを用いた傾きの推定の実装の経験はあるのでチャレンジします。
ただ、仰るとおり傾きを元にルールベースで足先の位置などを制御するのは難しそうですね。右前に傾いたら右前足の先を下げてそれ以外の足を上げるなどすればいいのかな？くらいしか見えていません。
しばらく試して難しそうなら強化学習に浮気してみようと思います。

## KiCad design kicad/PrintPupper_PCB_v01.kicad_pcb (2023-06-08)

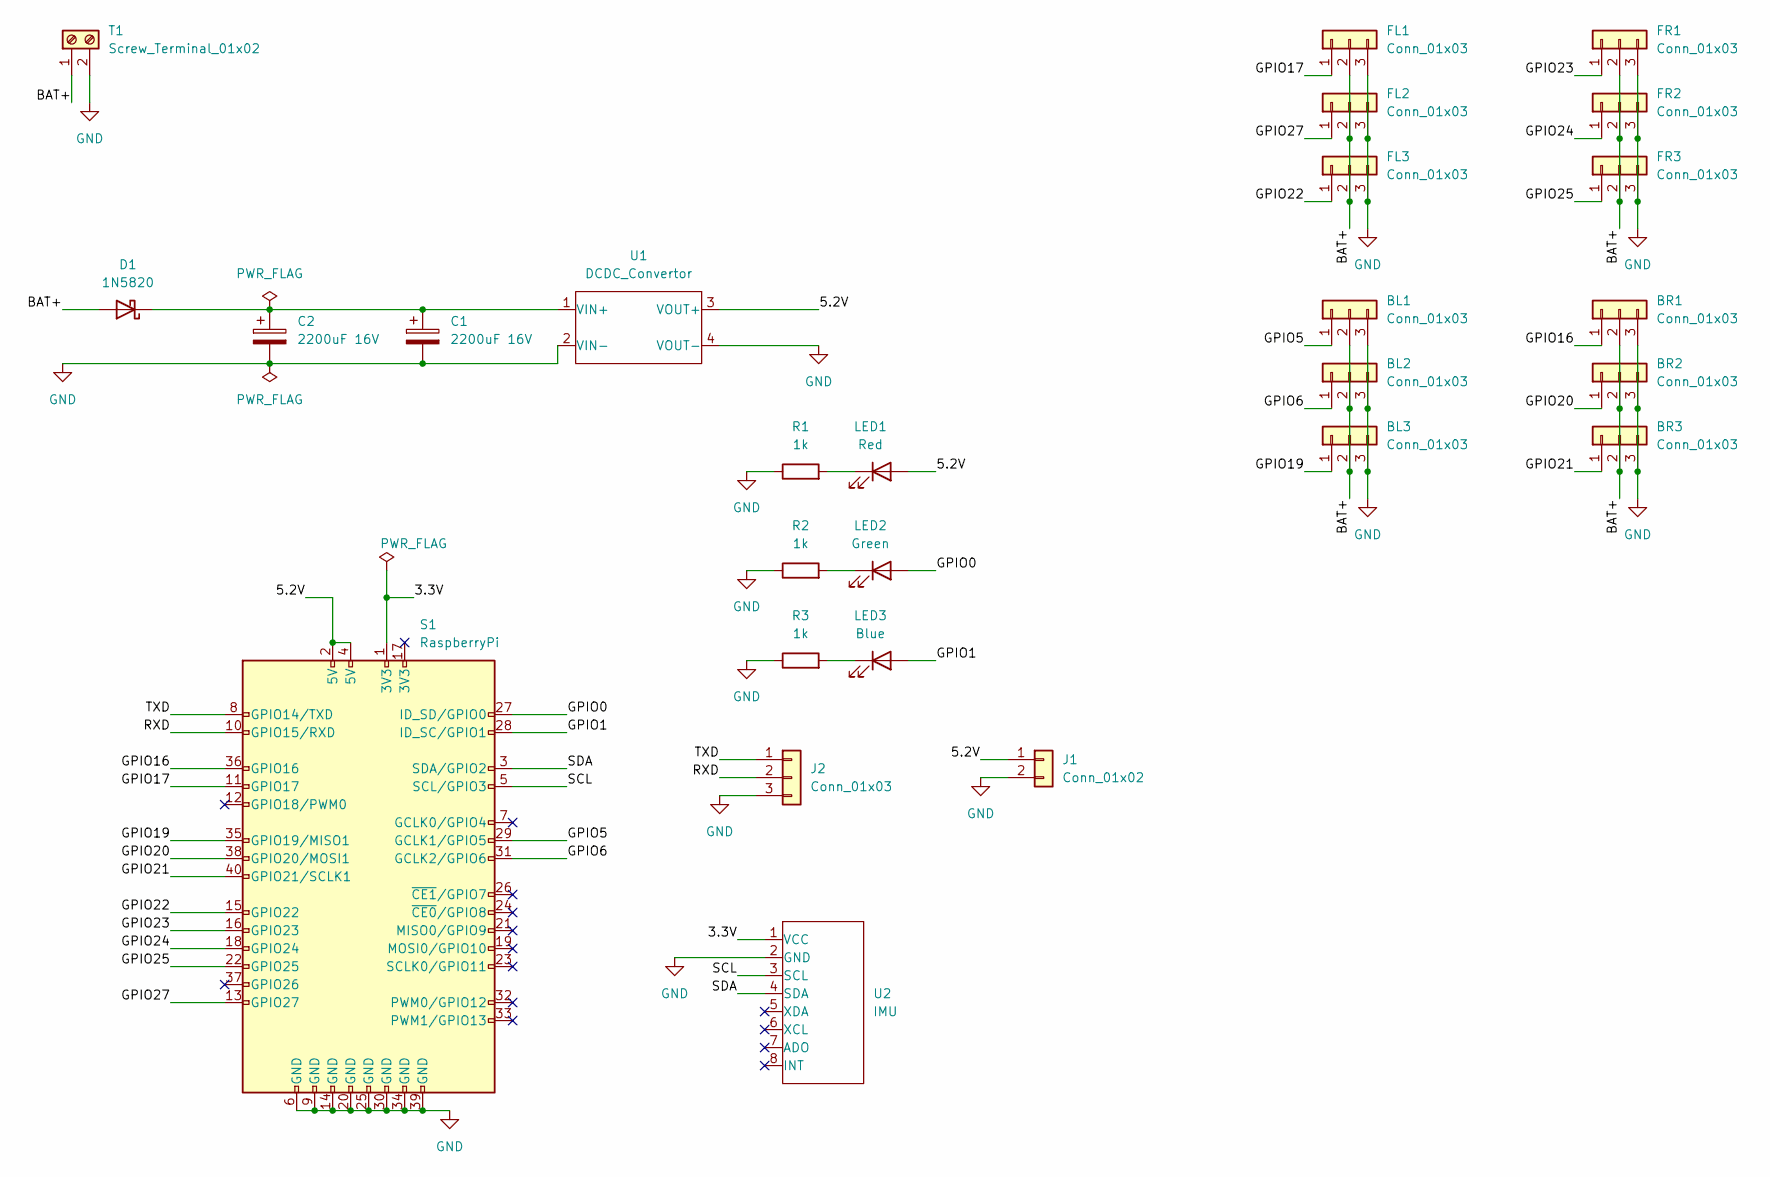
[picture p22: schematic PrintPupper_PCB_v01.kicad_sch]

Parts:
BL1, BL2, BL3: Conn_01x03; PinHeader_1x3P2.54mm
BR1, BR2, BR3: Conn_01x03; PinHeader_1x3P2.54mm
C1, C2: 2200uF 16V; CP_Radial_D10.0mm_P5.00mm
D1: 1N5820; D_DO-201AD_P5.08mm_Vertical_AnodeUp
FL1, FL2, FL3: Conn_01x03; PinHeader_1x3P2.54mm
FR1, FR2, FR3: Conn_01x03; PinHeader_1x3P2.54mm
J1: Conn_01x02; PinHeader_1x2P2.54mm
J2: Conn_01x03; PinHeader_1x3P2.54mm
LED1: Red; LED_D5.0mm
LED2: Green; LED_D5.0mm
LED3: Blue; LED_D5.0mm
R1, R2, R3: 1k; R_Axial_DIN0207_L6.3mm_D2.5mm_P2.54mm_Vertical
S1: RaspberryPi; PinSocket_2x20_P2.54mm_Vertical
T1: Screw_Terminal_01x02; TerminalBlock_2P5.08mm
U1: DCDC_Convertor; module_XL6009_dcdc
U2: IMU; imu_mpu6050

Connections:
/3.3V: S1.1 (3V3), U2.1 (VCC)
/5.2V: J1.1, LED1.2 (A), S1.2 (5V), S1.4 (5V), U1.3 (VOUT+)
/BAT+: BL1.2, BL2.2, BL3.2, BR1.2, BR2.2, BR3.2, D1.2 (A), FL1.2, FL2.2, FL3.2, FR1.2, FR2.2, FR3.2, T1.1
/GPIO0: LED2.2 (A), S1.27 (ID_SD/GPIO0)
/GPIO1: LED3.2 (A), S1.28 (ID_SC/GPIO1)
/GPIO5: BL1.1, S1.29 (GCLK1/GPIO5)
/GPIO6: BL2.1, S1.31 (GCLK2/GPIO6)
/GPIO16: BR1.1, S1.36 (GPIO16)
/GPIO17: FL1.1, S1.11 (GPIO17)
/GPIO19: BL3.1, S1.35 (GPIO19/MISO1)
/GPIO20: BR2.1, S1.38 (GPIO20/MOSI1)
/GPIO21: BR3.1, S1.40 (GPIO21/SCLK1)
/GPIO22: FL3.1, S1.15 (GPIO22)
/GPIO23: FR1.1, S1.16 (GPIO23)
/GPIO24: FR2.1, S1.18 (GPIO24)
/GPIO25: FR3.1, S1.22 (GPIO25)
/GPIO27: FL2.1, S1.13 (GPIO27)
/RXD: J2.2, S1.10 (GPIO15/RXD)
/SCL: S1.5 (SCL/GPIO3), U2.3 (SCL)
/SDA: S1.3 (SDA/GPIO2), U2.4 (SDA)
/TXD: J2.1, S1.8 (GPIO14/TXD)
GND: BL1.3, BL2.3, BL3.3, BR1.3, BR2.3, BR3.3, C1.2, C2.2, FL1.3, FL2.3, FL3.3, FR1.3, FR2.3, FR3.3, J1.2, J2.3, R1.1, R2.1, R3.1, S1.6 (GND), S1.9 (GND), S1.14 (GND), S1.20 (GND), S1.25 (GND), S1.30 (GND), S1.34 (GND), S1.39 (GND), T1.2, U1.2 (VIN-), U1.4 (VOUT-), U2.2 (GND)
unnamed: C1.1, C2.1, D1.1 (K), U1.1 (VIN+)
unnamed: LED1.1 (K), R1.2
unnamed: LED2.1 (K), R2.2
unnamed: LED3.1 (K), R3.2

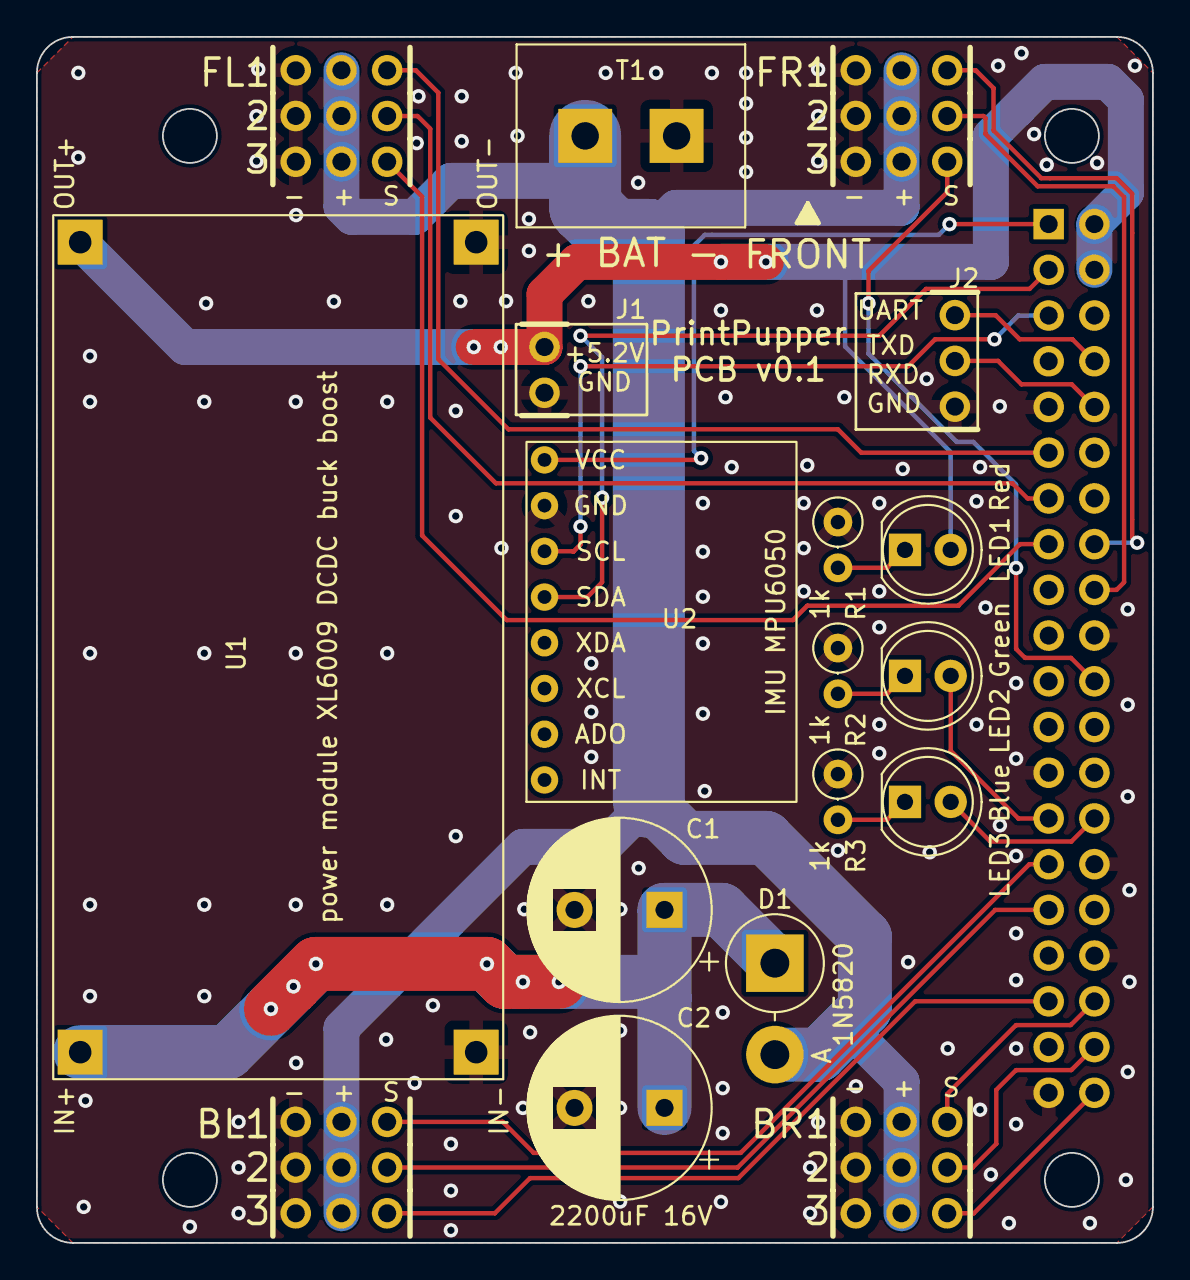
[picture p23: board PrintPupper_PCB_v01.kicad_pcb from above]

Board: 2 copper layers, 62.0 x 67.0 mm, 27 parts (1 on the bottom side), 26 nets.

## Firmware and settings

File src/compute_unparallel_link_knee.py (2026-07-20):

import math
from Config import Configuration

# 非平行リンク機構の計算をする、この計算内部はpupperのコアと表現型が異なるため入出力の取り扱いに注意
class compute_unparallel_link_knee:
    def __init__(self, config):
        # 非平行リンク機構パラメータ
        self.L1 = config.LEG_L1
        self.L2 = config.LEG_L2
        self.L3_offset = config.LEG_UNPRALLEL_L3
        self.L4 = config.LEG_UNPRALLEL_L4
        self.L5 = config.LEG_UNPRALLEL_L5
        self.ofstX = config.UNPRALLEL_ofstX
        self.ofstY = config.UNPRALLEL_ofstY
        print(f"L1={self.L1}, L2={self.L2}, L3_offset={self.L3_offset}, L4={self.L4}, L5={self.L5}, ofstX={self.ofstX}, ofstY={self.ofstY}")
        return

    def compute(self, theta_leg, theta_knee, mirror):
        # ミラー脚(右)なら角度を正負反転
        if mirror:
            theta_leg = -theta_leg
            theta_knee = -theta_knee

        # L1の終端座標（原点からのベクトル）
        x1 = self.L1 * math.cos(theta_leg)
        y1 = self.L1 * math.sin(theta_leg)

        # L2方向（L1から見て π - 内角だけ反時計回り）
        theta_L2 = theta_leg + (math.pi - theta_knee)

        # L2上のロッド接続点の位置（L3_offsetで任意）
        Px = x1 + self.L3_offset * math.cos(theta_L2)
        Py = y1 + self.L3_offset * math.sin(theta_L2)

        # サーボ3の位置（オフセット）
        x3 = self.ofstX
        y3 = self.ofstY

        # 求めたい角度 theta_s3 は、ロッド(L5)→リンク(L4)→原点
        # 三角形：P - サーボ3 - L4端点（この角度を求める）
        dx = Px - x3
        dy = Py - y3
        D = math.hypot(dx, dy)

        # 三角形の余弦定理
        cos_angle = (self.L4**2 + D**2 - self.L5**2) / (2 * self.L4 * D)
        if abs(cos_angle) > 1.0:
            return float('nan')  # 解なし

        angle_at_servo = math.acos(cos_angle)
        theta_line = math.atan2(dy, dx)

        # 2つあるうちの「L2方向に近い解」を選択
        theta_candidate1 = theta_line + angle_at_servo
        theta_candidate2 = theta_line - angle_at_servo

        # サーボホーン角度を選ぶ
        # 比較対象ベクトルは (cos(theta_L2), sin(theta_L2))
        v1 = (math.cos(theta_candidate1), math.sin(theta_candidate1))
        v2 = (math.cos(theta_candidate2), math.sin(theta_candidate2))
        target = (math.cos(theta_L2), math.sin(theta_L2))

        def dot(u, v): return u[0]*v[0] + u[1]*v[1]

        if dot(v1, target) > dot(v2, target):
            theta_s3 = theta_candidate1
        else:
            theta_s3 = theta_candidate2

        # ミラー脚(右)なら出力も反転
        if mirror:
            theta_s3 = -theta_s3

        return theta_s3





# 単体テスト、検算
# Unit testing, verification
if __name__=="__main__":
    _config = Configuration()
    culk = compute_unparallel_link_knee(_config)

    arg_leg_deg = 135
    arg_leg = math.radians(arg_leg_deg)
    arg_knee_deg = -89.9465
    arg_knee = math.radians(arg_knee_deg)
    arg_mirror = False
    theta_s3 = culk.compute(arg_leg, arg_knee, arg_mirror)
    print(f"compute_unparallel_link_knee( {arg_leg_deg}, {arg_knee_deg}, {arg_mirror}) = {math.degrees(theta_s3):6.4f}")

    arg_leg_deg = 126.87
    arg_leg = math.radians(arg_leg_deg)
    arg_knee_deg = -90
    arg_knee = math.radians(arg_knee_deg)
    arg_mirror = False
    theta_s3 = culk.compute(arg_leg, arg_knee, arg_mirror)
    print(f"compute_unparallel_link_knee( {arg_leg_deg}, {arg_knee_deg}, {arg_mirror}) = {math.degrees(theta_s3):6.4f}")

    arg_leg_deg = 143.13
    arg_leg = math.radians(arg_leg_deg)
    arg_knee_deg = -90
    arg_knee = math.radians(arg_knee_deg)
    arg_mirror = False
    theta_s3 = culk.compute(arg_leg, arg_knee, arg_mirror)
    print(f"compute_unparallel_link_knee( {arg_leg_deg}, {arg_knee_deg}, {arg_mirror}) = {math.degrees(theta_s3):6.4f}")

    arg_leg_deg = 151.997
    arg_leg = math.radians(arg_leg_deg)
    arg_knee_deg = -74.9299
    arg_knee = math.radians(arg_knee_deg)
    arg_mirror = False
    theta_s3 = culk.compute(arg_leg, arg_knee, arg_mirror)
    print(f"compute_unparallel_link_knee( {arg_leg_deg}, {arg_knee_deg}, {arg_mirror}) = {math.degrees(theta_s3):6.4f}")

    arg_leg_deg = -151.997
    arg_leg = math.radians(arg_leg_deg)
    arg_knee_deg = +74.9299
    arg_knee = math.radians(arg_knee_deg)
    arg_mirror = True
    theta_s3 = culk.compute(arg_leg, arg_knee, arg_mirror)
    print(f"compute_unparallel_link_knee( {arg_leg_deg}, {arg_knee_deg}, {arg_mirror}) = {math.degrees(theta_s3):6.4f}")

    arg_leg_deg = -126.65
    arg_leg = math.radians(arg_leg_deg)
    arg_knee_deg = 117.56
    arg_knee = math.radians(arg_knee_deg)
    arg_mirror = True
    theta_s3 = culk.compute(arg_leg, arg_knee, arg_mirror)
    print(f"compute_unparallel_link_knee( {arg_leg_deg}, {arg_knee_deg}, {arg_mirror}) = {math.degrees(theta_s3):6.4f}")

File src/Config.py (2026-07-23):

import numpy as np
from ServoCalibration import NEUTRAL_ANGLE_DEGREES
from enum import Enum
from pathlib import Path

# TODO: put these somewhere else
class PWMParams:
    def __init__(self):

# StanfordQuadruped pin assigen
#       self.pins = np.array([[2, 14, 18, 23], [3, 15, 27, 24], [4, 17, 22, 25]])
#       self.range = 4000
#       self.freq = 250

# PrintPupper pin assigen
#                               FR  FL  BR  BL
        self.pins = np.array([[ 23, 17, 16,  5], \
                              [ 24, 27, 20,  6], \
                              [ 25, 22, 21, 19]])

class ServoParams:
    def __init__(self):
        self.pwm_freq = 100

# If you choose 270deg servo, please "touch _servo_type_270deg"
# if enable "_servo_type_270deg"
        svflg = "_servo_type_270deg"
        file_path = Path(__file__).parent / svflg
        if file_path.is_file():
            self.pwm_usec_neutral = 1500
            self.pwm_usec_max = 1500 + 666
            self.pwm_usec_min = 1500 - 666
        else:
# default "_servo_type_180deg"
            svflg = "_servo_type_180deg"
            self.pwm_usec_neutral = 1500
            self.pwm_usec_max = 1500 + 1000
            self.pwm_usec_min = 1500 - 1000
        print(f"choose {svflg} rotate 1rad in PWM usec {self.pwm_usec_min} - {self.pwm_usec_neutral} - {self.pwm_usec_max}")

        self.pwm_usec_range = int(1000000 / self.pwm_freq)
        self.pwm_usec_per_rad = (self.pwm_usec_max - self.pwm_usec_min) / np.pi

        # The neutral angle of the joint relative to the modeled zero-angle in degrees, for each joint
        self.neutral_angle_degrees = NEUTRAL_ANGLE_DEGREES

# StanfordQuadruped rotate invert
#       self.servo_multipliers = np.array(
#           [[1, 1, 1, 1], [-1, 1, -1, 1], [1, -1, 1, -1]]
#       )

# PrintPupper rotate invert
#                                           FR FL BR BL
        self.servo_multipliers = np.array([[ 1, 1,-1,-1], \
                                           [-1, 1,-1, 1], \
                                           [ 1,-1, 1,-1]])

    @property
    def neutral_angles(self):
        return self.neutral_angle_degrees * np.pi / 180.0  # Convert to radians

class Configuration:
    def __init__(self):
        ################# CONTROLLER BASE COLOR ##############
        self.ps4_deactivated_color = {"red": 255, "blue": 0, "green": 0}
        self.ps4_activated_color = {"red": 0, "blue": 0, "green": 255}
        self.ps4_torot_color = {"red": 0, "blue": 255, "green": 0}
        self.ps4_calibration_color = {"red": 255, "blue": 0, "green": 255}

        ######################## GEOMETRY ######################
        self.LEG_FB = 0.100             # front-back distance from center line to leg axis
        self.LEG_LR = 0.045             # left-right distance from center line to leg plane
        self.ABDUCTION_OFFSET = 0.045   # distance from abduction axis to leg
        self.LEG_OPENING = 0.020        # distance from directly below to the open leg

        self.LEG_L1 = 0.110
        self.LEG_L2 = 0.120
        self.LEG_UNPRALLEL_L3 = 0.060
        self.LEG_UNPRALLEL_L4 = 0.050
        self.LEG_UNPRALLEL_L5 = 0.090
        self.UNPRALLEL_ofstX = -0.005
        self.UNPRALLEL_ofstY =  0.025

        #################### STANCE ####################
        self.delta_x = self.LEG_FB
        self.delta_y = self.LEG_LR + self.ABDUCTION_OFFSET + self.LEG_OPENING
        self.x_center_of_gravity = 0.007
        self.x_shift_front = self.x_center_of_gravity + 0.010
        self.x_shift_back =  self.x_center_of_gravity - 0.010
        self.default_z_ref = -0.165
        self.min_z_ref = self.default_z_ref
        self.max_z_ref = self.default_z_ref + 0.040
        self.z_delta_as_down_speed = 0.020
        self.z_delta_as_down_speed_rate = 0.4

        #################### COMMANDS ####################
        self.max_x_velocity = 0.28
        self.max_x_velocity_minus = 0.11
        self.max_y_velocity = 0.10
        self.max_yaw_rate = 1.0
        self.max_pitch = 18 * np.pi / 180.0
        self.max_pitch_as_trot = 7 * np.pi / 180.0

        #################### MOVEMENT PARAMS ####################
        self.z_time_constant = 0.02
        self.z_speed = 0.01  # maximum speed [m/s]
        self.pitch_deadband = 0.06
        self.pitch_time_constant = 0.25
        self.max_pitch_rate = 0.1
        self.roll_speed = 0.16  # maximum roll rate [rad/s]
        self.yaw_time_constant = 0.5
        self.max_stance_yaw = 0.2
        self.max_stance_yaw_rate = self.max_yaw_rate
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

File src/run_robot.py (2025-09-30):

import sys
import numpy as np
import time
from Controller import Controller
from JoystickInterface import JoystickInterface
from State import State
from HardwareInterface import HardwareInterface
from Config import Configuration
from Kinematics import four_legs_inverse_kinematics
from State import RState, State
from run_robot_caliblate_mode_2 import run_robot_caliblate_mode

def main(use_imu=False):
    # Create config
    config = Configuration()
    hardware_interface = HardwareInterface(config)

    # Create controller and user input handles
    controller = Controller(
        config,
        four_legs_inverse_kinematics,
    )
    state = State()
    print("Creating joystick listener...", end="")
    joystick_interface = JoystickInterface(config)
    print("Done.")

    # Wait until the activate button has been pressed
    joystick_interface.set_color(config.ps4_deactivated_color)
    while True:
        wait_loop = 0
        led_blink = 0

        print("Robot Waiting L1 button to activate robot")
        wait_loop_first = False
        while True:
            if (wait_loop % (25 if wait_loop_first else 100)) == 0:
                hardware_interface.set_led_green(bool(led_blink % 2))
                led_blink += 1
            wait_loop +=1
            command = joystick_interface.get_command(state)
            # PS4 gamepad from bluetooth mode as slow blink / USB gamepad as first blink
            if command.joy_ps4_usb:
                wait_loop_first = False
            else:
                wait_loop_first = True
            if command.activate_event == 1:
                break
            if command.caliblate_mode_event:
                command.caliblate_mode_event = False
                joystick_interface.set_color(config.ps4_calibration_color)
                run_robot_caliblate_mode(config, hardware_interface, joystick_interface)
                joystick_interface.set_color(config.ps4_deactivated_color)
                sys.exit()
            time.sleep(0.01)

        print("Robot Activate")
        hardware_interface.set_led_green(True)
        joystick_interface.set_color(config.ps4_activated_color)
        while True:
            d_time = time.time()

            # Parse the udp joystick commands and then update the robot controller's parameters
            command = joystick_interface.get_command(state)

            # Update PS4 Joystick LED, Update Onboard LED, Exit(to Deactivate) check
            if update_leds_loop_exit(config, state, command, hardware_interface, joystick_interface):
                break

            # Step the controller forward by dt
            controller.run(state, command)

            # Update the pwm widths going to the servos
            hardware_interface.set_actuator_positions(state.joint_angles)

            # cycle tune
            t_time = time.time()
            dt = (float)(t_time - d_time)
            dt_dt = (float)(config.dt - dt)
            dt_dt = round(dt_dt, 3)
            if (dt_dt > 0) and (dt_dt >= config.dt_min_sleep):
                time.sleep(dt_dt)

def update_leds_loop_exit(config, state, command, hardware_interface, joystick_interface):
    if command.activate_event:
        if state.now_state == RState.REST:
            print("Robot Deactivate")
            joystick_interface.set_color(config.ps4_deactivated_color)
            hardware_interface.set_led_blue(False)
            return True

    if command.trot_event:
        if state.now_state == RState.REST:
            joystick_interface.set_color(config.ps4_torot_color)
            hardware_interface.set_led_blue(True)
            print("Robot start Torot")
        else:
            joystick_interface.set_color(config.ps4_activated_color)
            hardware_interface.set_led_blue(False)
            print("Robot stop Torot")

    return False

if __name__ == "__main__":
    main()

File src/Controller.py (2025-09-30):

from Gaits import GaitController
from StanceController import StanceController
from SwingLegController import SwingController
from Utilities import clipped_first_order_filter
from State import RState, State

import numpy as np
from transforms3d.euler import euler2mat, quat2euler
from transforms3d.quaternions import qconjugate, quat2axangle
from transforms3d.axangles import axangle2mat

class Controller:
    """Controller and planner object
    """

    def __init__(
        self,
        config,
        inverse_kinematics,
    ):
        self.config = config

        self.smoothed_yaw = float(0)
        self.inverse_kinematics = inverse_kinematics

        self.hands_tick = int(0)
        self.hands_ticks = int(0)
        self.hands_switch_RL = int(0)
        self.hands_smoothed_yaw = float(0)
        self.hands_smoothed_push = float(0)

        self.contact_modes = np.zeros(4)
        self.gait_controller = GaitController(self.config)
        self.swing_controller = SwingController(self.config)
        self.stance_controller = StanceController(self.config)

        self.activate_transition_mapping =  {RState.DEACT:RState.REST,  RState.REST:RState.DEACT, RState.TROT:RState.TROT, RState.HANDS:RState.HANDS}
        self.trot_transition_mapping =      {RState.DEACT:RState.DEACT, RState.REST:RState.TROT,  RState.TROT:RState.REST, RState.HANDS:RState.HANDS}
        self.hands_transition_mapping =     {RState.DEACT:RState.DEACT, RState.REST:RState.HANDS, RState.TROT:RState.TROT, RState.HANDS:RState.REST}

    def step_gait(self, state, command):
        """Calculate the desired foot locations for the next timestep

        Returns
        -------
        Numpy array (3, 4)
            Matrix of new foot locations.
        """
        contact_modes = self.gait_controller.contacts(state.ticks)
        new_foot_locations = np.zeros((3, 4))
        for leg_index in range(4):
            contact_mode = contact_modes[leg_index]
            foot_location = state.foot_locations[:, leg_index]
            if contact_mode == 1:
                new_location = self.stance_controller.next_foot_location(leg_index, state, command)
            else:
                swing_proportion = (
                    self.gait_controller.subphase_ticks(state.ticks) / self.config.swing_ticks
                )
                new_location = self.swing_controller.next_foot_location(
                    swing_proportion,
                    leg_index,
                    state,
                    command
                )
            new_foot_locations[:, leg_index] = new_location
        return new_foot_locations, contact_modes


    def run(self, state, command):
        """Steps the controller forward one timestep

        Parameters
        ----------
        controller : Controller
            Robot controller object.
        """

        ########## Update operating state based on command ######
        state.pre_state = state.now_state
        if command.activate_event:
            state.now_state = self.activate_transition_mapping[state.now_state]
        elif command.trot_event:
            state.now_state = self.trot_transition_mapping[state.now_state]
        elif command.hands_event:
            state.now_state = self.hands_transition_mapping[state.now_state]

        if state.now_state == RState.TROT:
            state.foot_locations, contact_modes = self.step_gait(
                state,
                command,
            )

            # Apply the desired body rotation
            trot_rotated_foot_locations = (
                euler2mat(
                    command.roll, command.pitch, 0.0
                )
                @ state.foot_locations
            )

            # Construct foot rotation matrix to compensate for body tilt
            (roll, pitch, yaw) = quat2euler(state.quat_orientation)
            correction_factor = 0.8
            max_tilt = 0.4
            roll_compensation = correction_factor * np.clip(roll, -max_tilt, max_tilt)
            pitch_compensation = correction_factor * np.clip(pitch, -max_tilt, max_tilt)
            rmat = euler2mat(roll_compensation, pitch_compensation, 0)

            trot_rotated_foot_locations = rmat.T @ trot_rotated_foot_locations

            state.joint_angles = self.inverse_kinematics(
                trot_rotated_foot_locations, self.config
            )

        # 「お手」 HANDS 機能の追加 (REST は HANDS と共通の state_hands_proc に置き換え) -----
        elif state.now_state == RState.HANDS:
            # 右スティック or 上下高さ変更 の操作中は REST->HANDS 移行を拒否する
            if (state.pre_state == RState.REST and
                    (abs(command.pitch) >= self.config.pitch_deadband
                    or abs(command.yaw_rate) >= self.config.pitch_deadband)
                    or command.height != self.config.default_z_ref):
                state.now_state = RState.REST
                self.state_hands_proc(False, state, command)
            else:
                self.state_hands_proc(True, state, command)

        elif state.now_state == RState.REST:
            # 右スティック or PUSH の操作中は HANDS->REST 移行を拒否する
            if (state.pre_state == RState.HANDS and
                    (abs(command.pitch) >= self.config.pitch_deadband
                    or abs(command.yaw_rate) >= self.config.pitch_deadband
                    or command.hands_event_arg_PUSH)):
                state.now_state = RState.HANDS
                self.state_hands_proc(True, state, command)
            else:
                self.state_hands_proc(False, state, command)
        # --------------------------------------------------------------------------------

        state.ticks += 1
        state.pitch = command.pitch
        state.roll = command.roll
        state.height = command.height
        return

    def set_pose_to_rest(self, state, command):
        yaw_proportion = command.yaw_rate / self.config.max_yaw_rate
        self.smoothed_yaw += (
            self.config.dt
            * clipped_first_order_filter(
                self.smoothed_yaw,
                yaw_proportion * -self.config.max_stance_yaw,
                self.config.max_stance_yaw_rate,
                self.config.yaw_time_constant,
            )
        )
        # Set the foot locations to the default stance plus the standard height
        state.foot_locations = (
            self.config.default_stance
            + np.array([0, 0, command.height])[:, np.newaxis]
        )
        # Apply the desired body rotation
        rest_rotated_foot_locations = (
            euler2mat(
                command.roll,
                command.pitch,
                self.smoothed_yaw,
            )
            @ state.foot_locations
        )
        return rest_rotated_foot_locations
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

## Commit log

2023-06-08 PrintPupper for git public under construction
    [01_lower_leg_Left_2pcs.stl, 02_lower_leg_Right_2pcs.stl, 03_upper_leg_4pcs.stl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]
2023-06-08 amend PrintPupper_design.xlsx
    [PrintPupper_design.xlsx]
2023-09-10 add contents PrintPupper_design.xlsx
    [PrintPupper_design.xlsx]
2023-09-11 Raspberry Pi confirm of parts list amend.
    [PrintPupper_design.xlsx]
